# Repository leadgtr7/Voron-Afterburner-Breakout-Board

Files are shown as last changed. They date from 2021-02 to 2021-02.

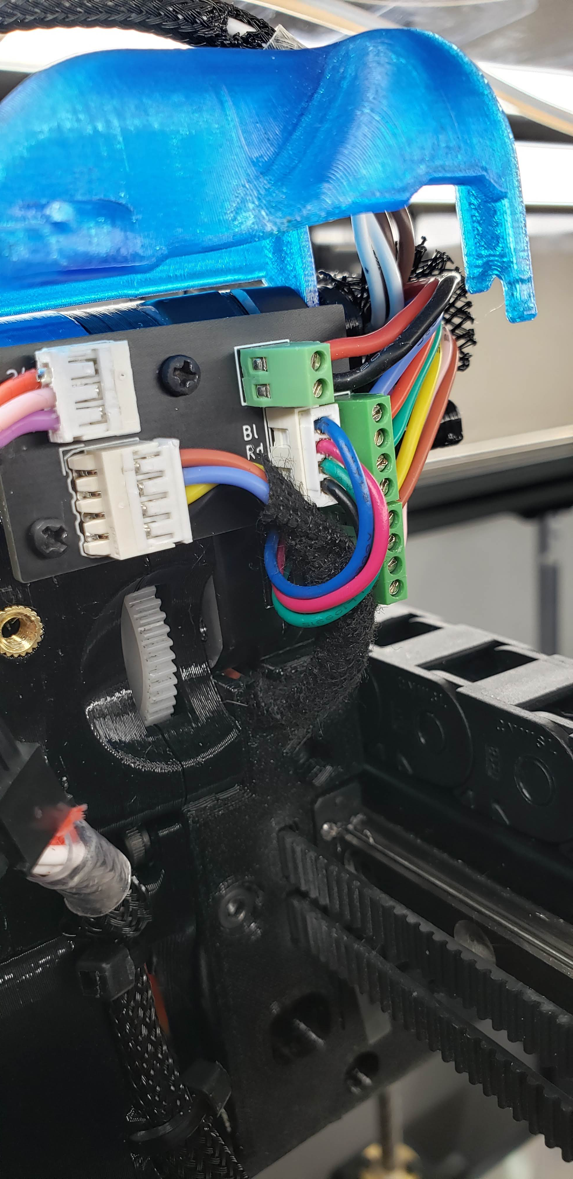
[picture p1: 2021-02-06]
Reference Photos/Assembly Pic2.jpg

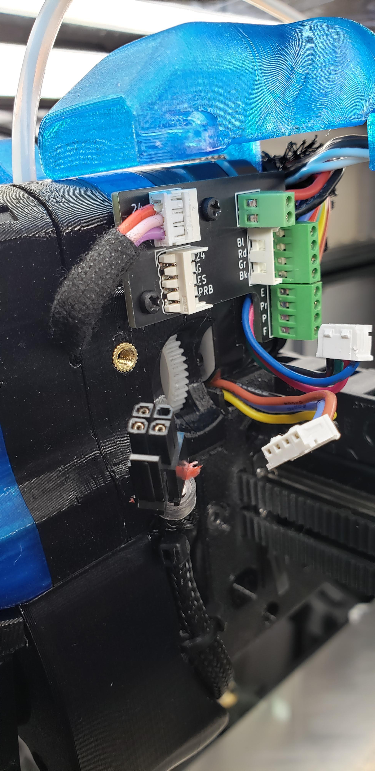
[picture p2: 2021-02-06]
Reference Photos/Assembly Pic1.jpg

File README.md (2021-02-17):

# Voron-Afterburner-Breakout-Board
This is a breakout board for use with the Voron Afterburner toolhead. 
Typically there would be the following wires for the tool head
2 for Hot End Fan
2 For Part Fan
4 For Stepper
2 For thermistor
2 For Heater
3 For Probe
2 For Endstop
for a total of 17 wires

This Board removes reduntant connection across the tool head and thus reduces the number of wires in the cable chain to 14

I have only used this board with an SKRv1.3

If you use a different board you will need to make sure that your board switches the fans on the ground side (ie common 24v).

This does not replace the need for a BAT-85 (or similar schottky diode) on the probe output. Could probably add to the board but space is already really tight.

You will find a spreadsheet with all the wiring colors and info here as well as a part BOM
https://github.com/leadgtr7/Voron-Afterburner-Breakout-Board/blob/main/Voron%20Toolhead%20Breakout%20Board.xlsx
https://github.com/leadgtr7/Voron-Afterburner-Breakout-Board/blob/main/AB%20BOB%20Wiring%20Diagram.pdf

kicad files are here
https://github.com/leadgtr7/Voron-Afterburner-Breakout-Board/tree/main/kicad%20Project

gerbers zipped and ready for your favorite pcb manufacturer are here (I used JLCPCB with a matte black silkscreen)
https://github.com/leadgtr7/Voron-Afterburner-Breakout-Board/tree/main/gerbers

you will need to reprint 2 peices from the clockwork as they include standoffs for the pcb here
https://github.com/leadgtr7/Voron-Afterburner-Breakout-Board/tree/main/Modified%20Clockwork%20Parts

Optional: I also modified the chain anchor to add a zip tie for strain relief on the wires

In addition you will need 2 M2x6mm screws. I used machine screws and wouldn't recommend using the standard voron M2 plastic screws as they are too long

I have also uploaded some pictures of the board installed on the toolhead here. Make sure to trim the leads on the terminal blocks down as the may short on the motor body!
https://github.com/leadgtr7/Voron-Afterburner-Breakout-Board/tree/main/Reference%20Photos

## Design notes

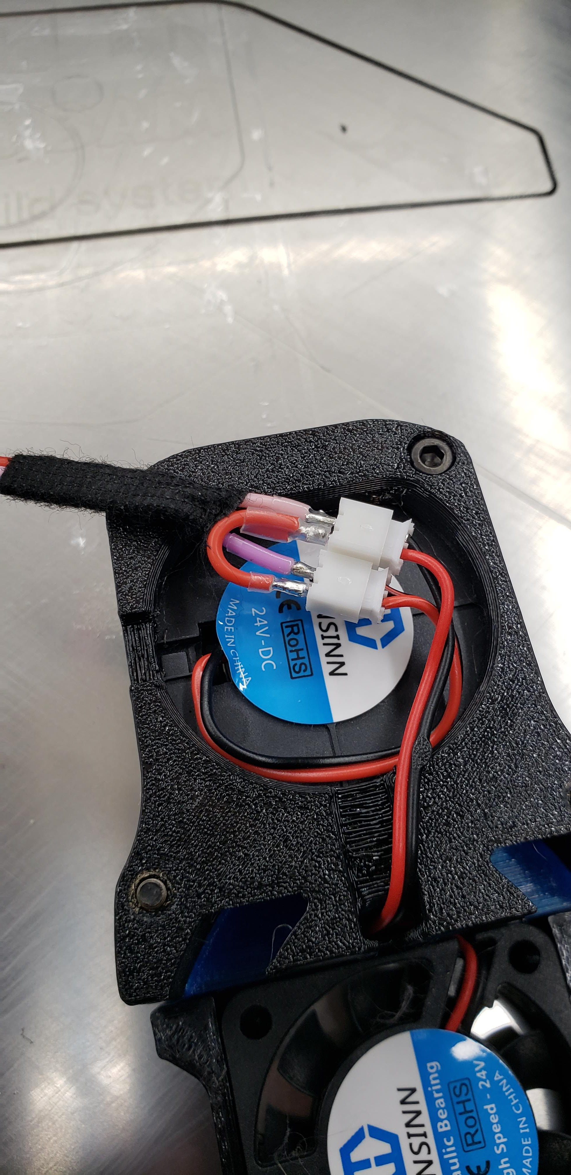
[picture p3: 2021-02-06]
Reference Photos/Part and Hot End Fan 24V Connection.jpg

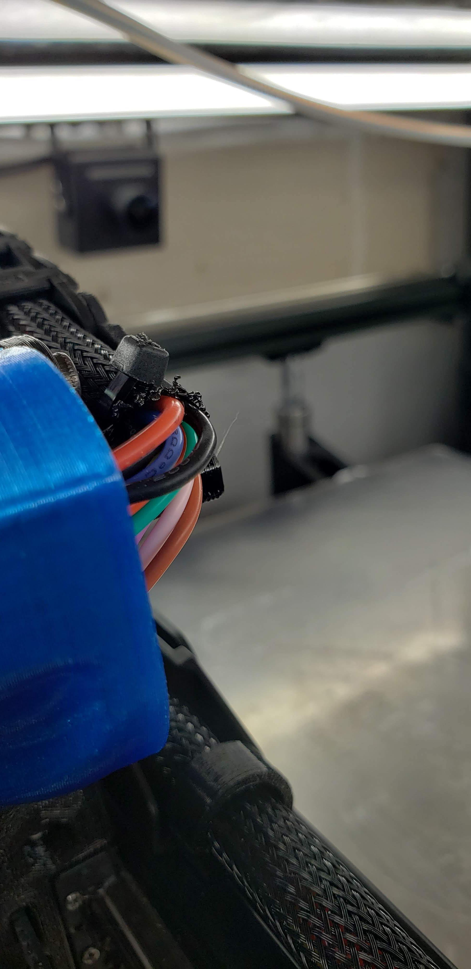
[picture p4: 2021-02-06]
Reference Photos/Modifed Cable Carrier With Zip Tie Mount.jpg

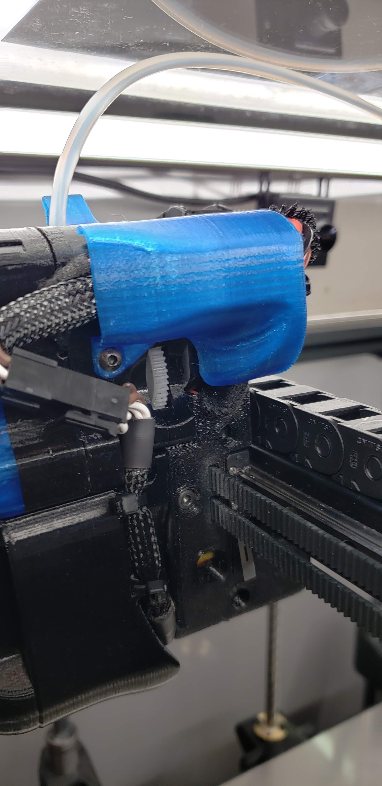
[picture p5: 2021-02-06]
Reference Photos/Cover Closed.jpg

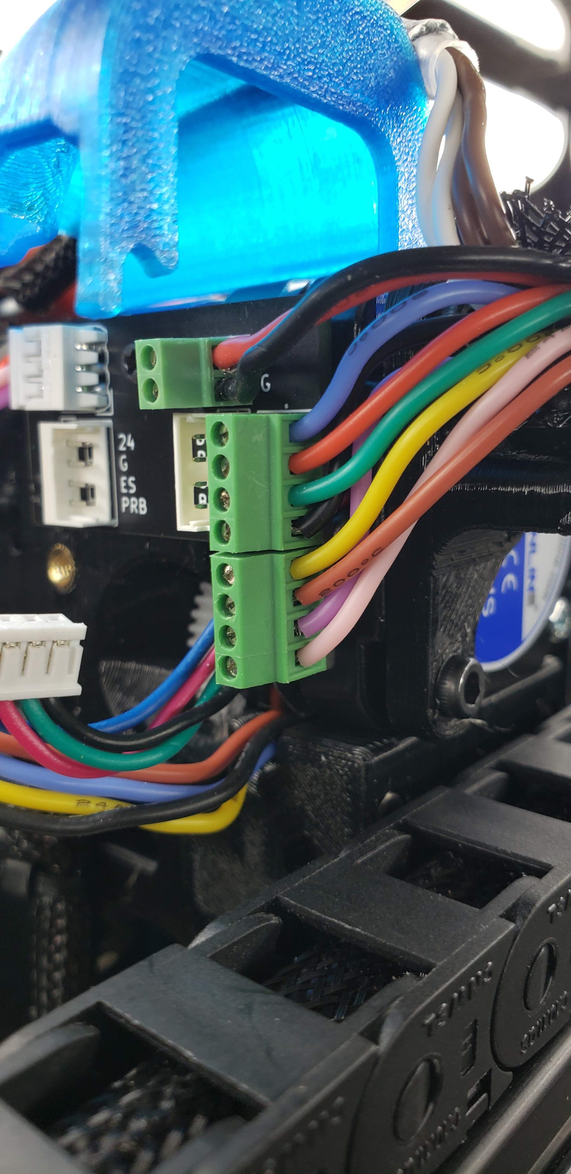
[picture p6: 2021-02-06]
Reference Photos/From Back View of Terminal Blocks.jpg

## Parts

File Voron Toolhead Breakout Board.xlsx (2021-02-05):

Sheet: BreakoutBoardWiring
Wiring List
 |  | These are the wires for each of the components |  |  |  |  |  | These are the wires that run in the cable chain (ie the terminal blocks on the BOB)
Connection | BOB Connectors Silkscreen Reference | Voltage | Wire Gauge | Wire Color | Notes About Component Side | Connector | Pin | Cable Chain Wire Gauge | Cable Chain Wire Color | Notes About Cable Chain Side | Cable Chain Terminal Block top 4 position is A and bottom 4 position is B | TB Position (Top is Pin 1) | BOB Terminal Block Silkscreen Reference
Hotend Cooling Fan | F | +24V | 24 | Red | Fan + and Part + need to be connected together in the space behind the 4020 part cooling fan before coming out of the wiring opening | MircoLatch 3 | 3 | N/A | N/A |  | N/A | N/A | N/A
Hotend Cooling Fan | N/A | Sw Gnd | 24 | Pink |  | MircoLatch 3 | 2 | 24 | Pink |  | B | 4 | F
Part Fan | P | +24V | 24 | Red | Fan + and Part + need to be connected together in the space behind the 4020 part cooling fan before coming out of the wiring opening | N/A | N/A | N/A | N/A |  | N/A | N/A | N/A
Part Fan | N/A | Sw Gnd | 24 | Purple |  | MircoLatch 3 | 1 | 24 | Purple |  | B | 3 | P
Heater | N/A | +24V | 20 | Brown |  | N/A | N/A | 20 | Brown | These wires don't go through the BOB. You should be able to route them so they come out the front and connect to the hotend | N/A | N/A | N/A
Heater | N/A | GND | 20 | Brown |  | N/A | N/A | 20 | Brown |  | N/A | N/A | N/A
Therm | N/A | 1 | 24 | White |  | N/A | N/A | 24 | White |  | N/A | N/A | N/A
Therm | N/A | 2 | 24 | White |  | N/A | N/A | 24 | White |  | N/A | N/A | N/A
Probe | 24 | +24V | 24 | Brown |  | MircoLatch 4 | 4 | N/A |  | Uses common power connections | N/A | N/A | N/A
Probe | G | GND | 24 | Blue |  | MircoLatch 4 | 3 | N/A |  | Uses common power connections | N/A | N/A | N/A
Probe | PRB | Signal | 24 | Black | This will be changing color to brown at Cable Chain Side | MircoLatch 4 | 1 | 24 | Brown | Note the color change here. this is so that Black can be used for stepper A+ | B | 2 | Pr
Endstop | ES | 1 | 24 | Yellow |  | MircoLatch 4 | 2 | 24 | Yellow |  | B | 1 | E
Endstop | N/A | GND | 24 | Yellow (Doesn't really matter) | This needs to be tied to ground on the probe before exited the wiring channel on the carriage | N/A | N/A | N/A | N/A | Uses common power connections | N/A | N/A | N/A
Stepper | Bk | A+ | 24 | Black |  | MircoLatch 4 | 1 | 24 | Black |  | A | 4 | Wasn't room for marking on pcb. Refer to the connector to the left for color coding as they are the same. Top to bottom are as follows; Blue, Red, Green, Black
Stepper | Gr | A- | 24 | Green |  | MircoLatch 4 | 2 | 24 | Green |  | A | 3
Stepper | Rd | B+ | 24 | Red |  | MircoLatch 4 | 3 | 24 | Red |  | A | 2
Stepper | Bl | B- | 24 | Blue |  | MircoLatch 4 | 4 | 24 | Blue |  | A | 1
Power +24V | N/A | +24V | N/A | N/A |  | N/A | N/A | 20 | Red | These are common connections for power and ground and are used for various items as noted | 2 Position | 1 | 24
Power GND | N/A | GND | N/A | N/A |  | N/A | N/A | 20 | Black |  |  | 2 | G

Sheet: BOM
Item | Manufacturer | P/N | Link | Qty | Notes
Micro Latch 4 Pos Vertical | Molex | 532530470 | https://www.digikey.com/en/products/detail/molex/0532530470/965998 | 1
Micro Latch 4 Pos Housing | Molex | 510650400 | https://www.digikey.com/en/products/detail/molex/0510650400/403568 | 2
Crimp Pins 22-26AWG | Molex | 503728000 | https://www.digikey.com/en/products/detail/molex/0503728000/2421920 | at least 11 | These aren't used on any of the 20 awg wires, get a bunch of these as they are tricky to crimp and you will butcher the first few you do (at least I did lol )
Micro Latch 3 Pos Horizontal | Molex | 532540370 | https://www.digikey.com/en/products/detail/molex/0532540370/1952199 | 1
Micro Latch 4 Pos Horizontal | Molex | 532540470 | https://www.digikey.com/product-detail/en/molex/0532540470/WM19001-ND/1952200 | 1
Micro Latch 3 Pos Housing | Molex | 510650300 | https://www.digikey.com/product-detail/en/molex/0510650300/WM19010-ND/403567 | 1
2 Position Terminal Block 2.54mm spacing |  |  | https://www.amazon.com/gp/product/B07YK4QM9C/ref=ppx_yo_dt_b_search_asin_title?ie=UTF8&psc=1 | 1
4 Position Terminal Block 2.54mm spacing |  |  | https://www.amazon.com/gp/product/B07WR5NMWN/ref=ppx_yo_dt_b_search_asin_title?ie=UTF8&psc=1 | 2

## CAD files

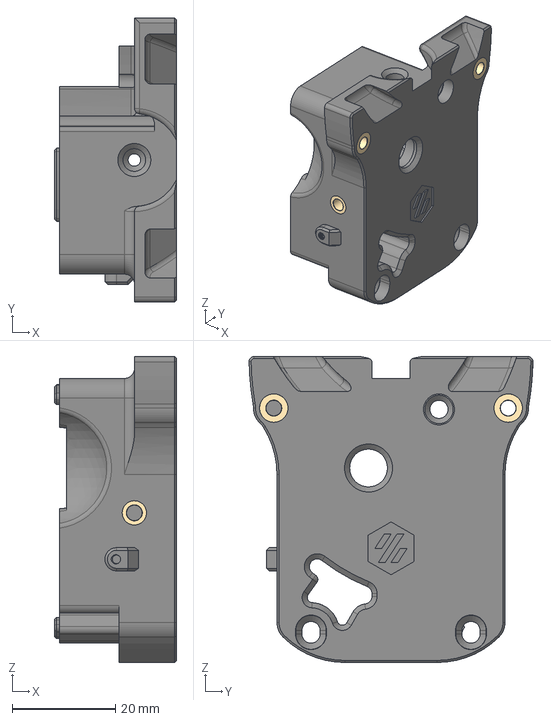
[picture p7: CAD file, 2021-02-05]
Modified Clockwork Parts/Main Body.step
23.7 x 55.0 x 59.3 mm
M3 Threaded Insert Short v1 x 4

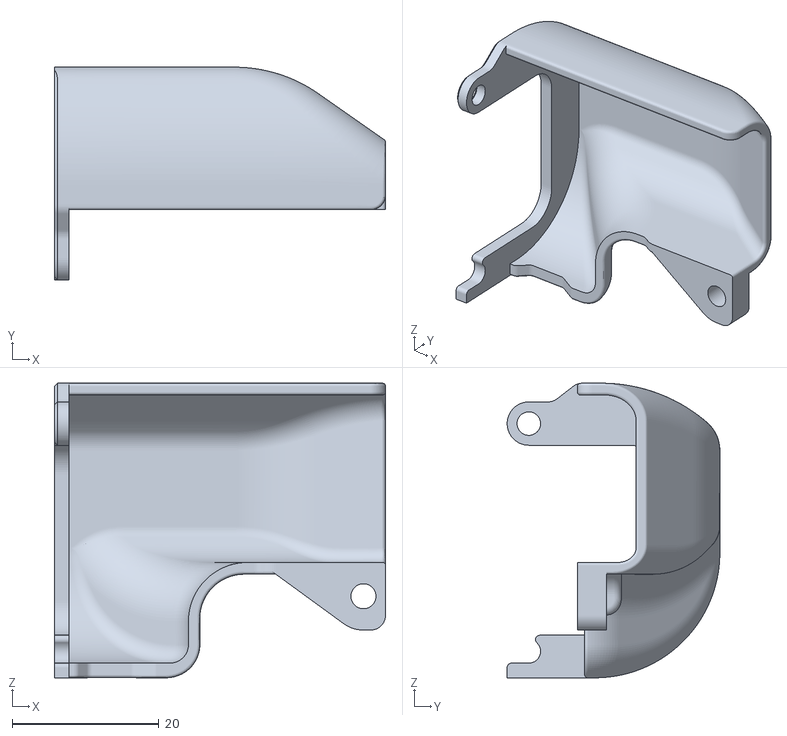
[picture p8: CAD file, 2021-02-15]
Modified Clockwork Parts/Connector_Cover_V1.8_LargerOpening.stl
45.1 x 29.0 x 40.1

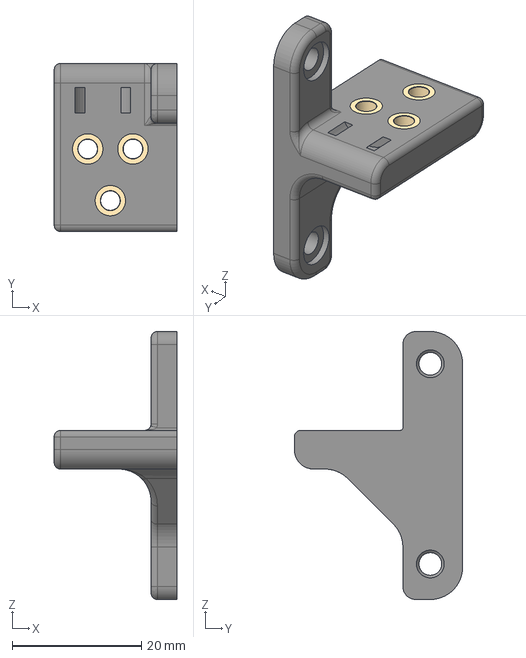
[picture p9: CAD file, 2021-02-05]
Modified Clockwork Parts/Chain Anchor - Generic.step
19.0 x 26.1 x 41.5 mm
M3 Threaded Insert Short v1 x 3

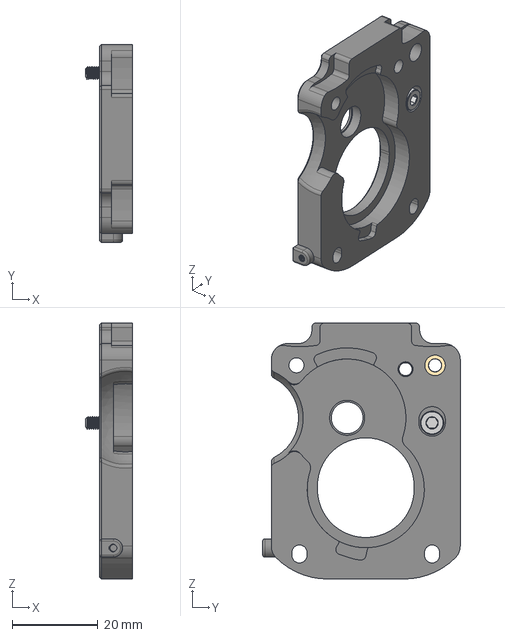
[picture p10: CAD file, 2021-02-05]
Modified Clockwork Parts/Motor Plate.step
11.0 x 46.2 x 59.9 mm
91290A113_M3x8 SHCS v2
M3 Threaded Insert Short v1 x 2

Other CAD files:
Modified Clockwork Parts/Chain Anchor - Generic.stl
Modified Clockwork Parts/MainBody.stl
Modified Clockwork Parts/Motor-Plate.stl

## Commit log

2021-02-05 first uploads
    [Main Body.step, Motor Plate.step, Motor Plate.stl]
2021-02-05 add cable chain anchor
    [Chain Anchor - Generic.step, Chain Anchor - Generic.stl]
2021-02-05 corrected STLs
    [MainBody.stl, Motor Plate.stl, Motor-Plate.stl]
2021-02-15 Create Connector_Cover_V1.8_LargerOpening.stl
    modified connection cover to give more room at back
    [Connector_Cover_V1.8_LargerOpening.stl]
2021-02-17 Create AB BOB Wiring Diagram.pdf
    Add wiring diagram
